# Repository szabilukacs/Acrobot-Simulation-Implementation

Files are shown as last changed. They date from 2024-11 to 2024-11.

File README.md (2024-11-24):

# Acrobot Simulation and Implementation

This repository contains the code and resources for my university thesis, which focused on the simulation and implementation of an **Acrobot** system. The Acrobot is a two-link underactuated robotic arm, commonly used in control theory research. This project bridges theoretical simulations with practical hardware implementation, showcasing the swing-up and stabilization of the Acrobot using Linear-Quadratic Regulator (LQR) control.

https://github.com/user-attachments/assets/334cb275-21a1-4bce-92d3-f9c4527cbd75

---

## 📖 Table of Contents

- [Project Structure](#-project-structure)
- [Features](#️-features)
- [Screenshots and Visuals](#-screenshots-and-visuals)
- [Getting Started](#-getting-started)
- [Results](#-results)
- [Further Details](#-further-details)

---

## 📂 Project Structure

### 1. **Simulations**
   - **Acrobot Swing-Up and Balance Simulation**:
     - A detailed MATLAB/Simulink simulation of the Acrobot, featuring:
       - The ability to modify system attributes, such as:
         - Adding noise to the system to test robustness.
         - Observing simulated data versus simulated encoder data and their differences.
       - A DC motor model implemented in the simulation.
       - Customizable starting positions for the Acrobot.
     - Parameters for the simulation are derived from real-world measurements, but they can be adjusted as needed.

   - **Theoretical Double Pendulum Simulation**:
     - Simulates a theoretical double pendulum to explore its chaotic dynamics and provide insights into the physics and mathematics of such systems.

### 2. **Arduino Implementations**
   - **Encoder Computing**:
     - Reads encoder values to measure the angles of the Acrobot's links in real-time.
   - **Servo Motor Control**:
     - Controls the torque applied to the Acrobot's actuator using a servo motor (replacing the DC motor used in the simulation).
   - **Combined Computing**:
     - Integrates encoder readings and motor control for a closed-loop system in hardware.

---

## 🛠️ Features

- **Simulink Models**: A modular and interactive simulation environment for testing and refining the Acrobot control system.
- **MATLAB Scripts**: Key functionalities include LQR design, energy calculations, and visualization.
- **Hardware Control**:
  - Arduino code for real-time encoder data processing and servo motor actuation.
- **Customization**:
  - Modify system parameters (e.g., masses, lengths, and moments of inertia) based on hardware measurements.
  - Test different starting positions for the Acrobot.

---

## 📸 Screenshots and Visuals

### Simulink Model

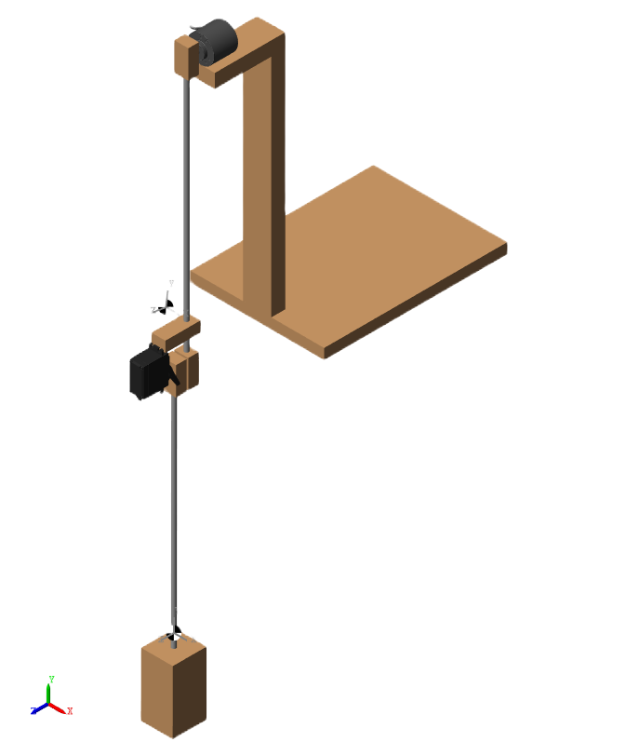
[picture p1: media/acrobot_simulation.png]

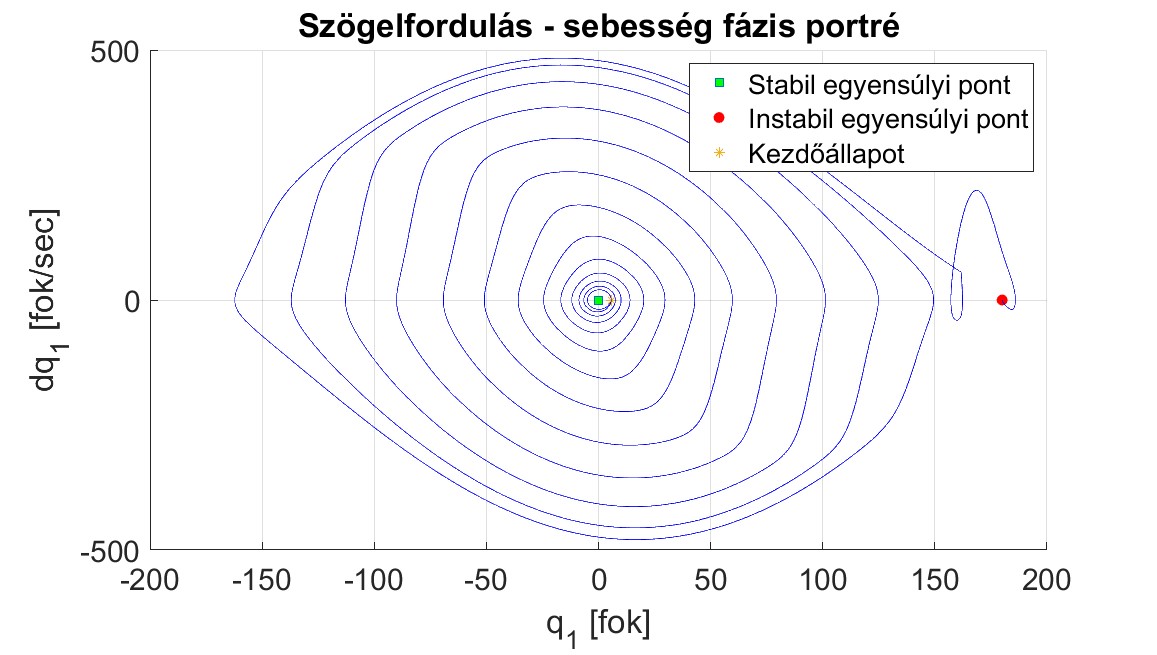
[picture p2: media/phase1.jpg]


### Implementation Setup
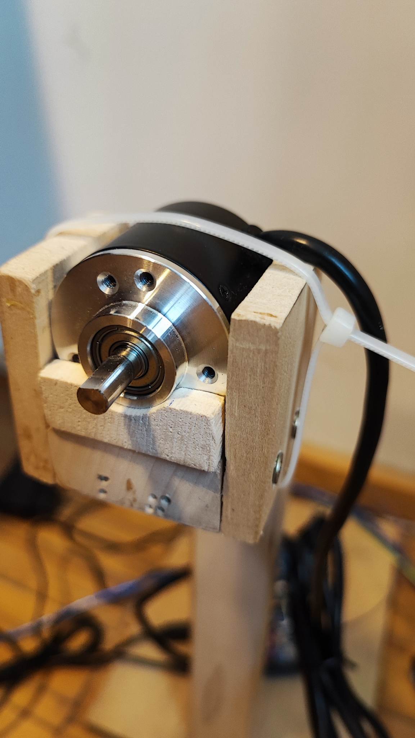
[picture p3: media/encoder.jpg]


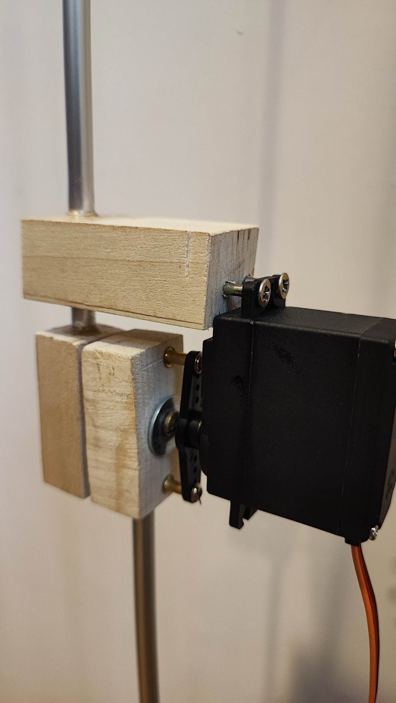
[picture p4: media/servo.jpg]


---

## 🚀 Getting Started

To run the simulation, execute the `main.m` script in MATLAB. This will:
1. Load the system parameters derived from real-world measurements.
2. Linearize the system around the operating point.
3. Perform LQR calculations.
4. Simulate the Acrobot swing-up and balancing behavior in Simulink.
5. Generate visualization plots for analysis.

---

## 📊 Results

### Features of the Simulation
- Observe both ideal simulated data and noisy encoder-like simulated data to analyze differences.
- Test and tune the system under various starting conditions and parameters.

### Hardware Validation
- Parameters in the simulation are based on real-world measurements to ensure accuracy.
- While the simulation uses a DC motor model, the implementation uses a servo motor for torque control.
- The implementation closely follows the behavior predicted by the simulation.

---

## 📜 Further Details

For an in-depth explanation of the project, including theoretical background, implementation details, and results, refer to the thesis document: **`Allamvizsga_szakdolgozat.pdf`**.

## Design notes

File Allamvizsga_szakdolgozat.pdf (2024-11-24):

## UNIVERSITATEA „SAPIENTIA” DIN CLUJ-NAPOCA

FACULTATEA DE ȘTIINȚE TEHNICE ȘI UMANISTE,

## TÎRGU MUREȘ

### SPECIALIZAREA AUTOMATICĂ ȘI INFORMATICĂ APLICATĂ

# REGLAREA ȘI IMPLEMENTAREA PRACTICĂ A UNUI ACROBOT

# PROIECT DE DIPLOMĂ

Coordonator științific: | Absolvent:
Prof.dr.ing. Dávid László | Lukács Szabolcs

2023

UNIVERSITATEA „SAPIENTIA” din CLUJ-NAPOCA | Viza facultății:
Facultatea de Științe Tehnice și Umaniste din Târgu Mureș
Specializarea: Automatică și informatică aplicată
LUCRARE DE DIPLOMĂ
Coordonator științific:
ș.l. dr. ing. Nume cadru didactic

Candidat: Nume student
Anul absolvirii: 2023
a) Tema lucrării de licență:
CONTROLUL AUTOMAT AL SERELOR
b) Problemele principale tratate:
- Studiu bibliografic privind sistemele de reglare.
- Realizarea unei aplicații pentru simularea procesului studiat.
- Clasificarea metodelor de reglare
c) Desene obligatorii:
- Schema bloc al aplicației
- Diagrame UML privind software-ul realizat.
d) Softuri obligatorii:
-Aplicație
e) Bibliografia recomandată:
- Márton Lőrinc, Irányítsátechnika, Scientia, 2009
- Dávid László, Tehnici de optimizare: metode numerice de calcul în tehnica reglării optimale, Editura Universității Petru Maior, Tg. Mureș, 2000,
f) Termene obligatorii de consultații: săptămânal
g) Locul și durata practicii: Universitatea „Sapientia” din Cluj-Napoca, Facultatea de Științe Tehnice și Umaniste din Târgu Mureș
Primit tema la data de: 31.03.2022
Termen de predare: 27.06.2023
Semnătura Director Departament

Semnătura responsabilului
programului de studiu

Semnătura coordonatorului

Semnătura candidatului

Declarație

Subsemnatul Lukács Szabolcs, absolvent(ă) al/a specializării automatică şi informatică aplicată, promoția 2023 cunoscând prevederile Legii Educației Naționale 1/2011 și a Codului de etică și deontologie profesională a Universității Sapientia cu privire la furt intelectual declar pe propria răspundere că prezenta lucrare de licență/proiect de diplomă/disertație se bazează pe activitatea personală, cercetarea/proiectarea este efectuată de mine, informațiile și datele preluate din literatura de specialitate sunt citate în mod corespunzător.

Localitatea, Târgu Mureș
Data: 25.06.2023 | Absolvent
| Semnătura |

# REGLAREA ȘI IMPLEMENTAREA PRACTICĂ A UNUI ACROBOT Extras

Tema tezei mele este implementarea unui sistem de control dinamic neliniar subactuat, și anume un "ACROBOT", care poate fi folosit ca exercițiu de laborator. Controlul sistemelor subactuate necesită un tip de control diferit față de cel al sistemelor convenționale. Scopul meu este de a construi un mecanism experimental pentru a demonstra un astfel de control.

Sistemul dinamic studiat este "acrobotul", care este un pendul dublu inversat, dar care are un dispozitiv de intervenție doar în a doua articulație, deci are două grade de libertate, dar poate interveni doar într-unul dintre gradele de libertate, adică este subactuat.

Scopul principal al controlului este de a muta acrobotul din punctul de echilibru inferior, stabil, în punctul de echilibru superior, instabil, și de a-l stabiliza acolo cu ajutorul unui algoritm de control DLQR. Prin modelarea și simularea precisă a sistemului real, am obținut traiectoria prescrisă a celui de-al doilea segment. Pentru a pune în aplicare acest lucru on-line, adică în timp real, am utilizat o rețea neuronală pentru a mă asigura că unghiul prescris este obținut pe baza stărilor în timp real.

În implementare am folosit un servomotor pentru a deplasa al doilea segment și un encoder incremental pentru a măsura unghiurile și vitezele unghiulare. Prelucrarea semnalului și calcularea semnalului de acțiune se realizează cu ajutorul unor plăci de dezvoltare arduino conectate în rețea.

# SAPIENTIA ERDÉLYI MAGYAR TUDOMÁNYEGYETEM

## MAROSVÁSÁRHELYI KAR AUTOMATIKA ÉS ALKALMAZOTT INFORMATIKA SZAK

# ACROBOT SZABÁLYOZÁSA ÉS GYAKORLATI MEGVALÓSÍTÁSA

# DIPLOMADOLGOZAT

Témavezető: | Hallgató:
Dr. Dávid László, egyetemi tanár | Lukács Szabolcs

2023

# Kivonat

A dolgozatom témája egy olyan nemlineáris, alulaktuált dinamikus rendszer szabályozásának megvalósítása, nevezetesen egy „ACROBOT”, amelyet később laborgyakorlatként is lehet majd használni. Az alulaktuált rendszerek szabályozása másfajta szabályozást igényel, mint a hagyományos rendszereké. Célom egy olyan kísérleti eszköz elkészítése, amin be lehet mutatni egy ilyen szabályozást.

Az tanulmányozott dinamikus rendszer az „acrobot”, ami egy inverz dupla inga, de csak a 2. csuklóban van beavatkozó eszköz, tehát két szabadságfokkal rendelkezik, de csak az egyik szabadságfokban lehet beavatkozni, vagyis alulaktuált.

A szabályozás fő célja eljuttatni az acrobotot az alsó, stabil egyensúlyi pontjáról, a felső, instabil pontjára, és ott stabilizálni felhasználva egy DLQR szabályozási algoritmust. A valós rendszert pontosan modellezve, és szimulálva megkaptam a második szegmens előírt pályáját. Ahhoz, hogy ezt on-line, azaz valós időben lehessen implementálni, egy neuronálót használtam fel, amely biztosítja, hogy a valós idejű állapotok alapján kapjuk meg az előírt szöget.

A megvalósítás során egy szervomotort használok a második szegmens mozgatására, és egy inkrementális enkódert, a szögek és szögsebességek mérésére. A jelek feldolgozása és a beavatkozó jel kiszámítása hálózatba csatolt arduino fejlesztőlapokkal történik.

Kulcsszavak: Acrobot, Alulaktuált rendszer, LQR

# Abstract

The topic of my thesis is the implementation of a nonlinear underactuated dynamic control system, namely an "ACROBOT", which can be used as a laboratory exercise. The control of underactuated systems requires a different kind of control than that of conventional systems. My goal is to build an experimental device to demonstrate such a control.

The dynamic system under study is the "acrobot", which is an inverted double pendulum, but it has an intervention device only in the 2nd joint, so it has two degrees of freedom, but it can only intervene in one degree of freedom, i.e., it is underactuated.

The main purpose of the control is to move the acrobot from its lower, stable equilibrium point to its upper, unstable point and stabilize it there using a DLQR control algorithm. By accurately modeling and simulating the real system, I obtained the prescribed trajectory of the second segment. In order to implement this on-line, in real time, I used a neural network to ensure that the prescribed angle is obtained based on the real-time states.

In the implementation, I use a servo motor to move the second segment and an incremental encoder to measure the angles and angular velocities. The signal processing and the calculation of the action signal is done with networked arduino development boards.

Keywords: Acrobot, Underactuated Systems, LQR

## Tartalomjegyzék

### 10 ÖSSZEGZÉS, KÖVETKEZTETÉSEK | 51 11 IRODALOMJEGYZÉK | 53 12 FÜGGELÉK | 55

## 1 Ábrajegyzék

4.1. ábra. Az acrobot modellje [4] | 13
4.2. ábra. Az Acrobot optimális pályája | 16
5.1. ábra. A szabályzás tömbvázlata[10, p. 12] | 17
5.2. ábra. A nyílt rendszer instabil pólusai | 19
5.3. ábra. A zárt rendszer stabil pólusai | 21
5.4. ábra. A rendszer állapotai szimuláció közben | 22
6.1. ábra. Egy rétegű, egy neuront tartalmazó neuronháló felépítése, az aktivációs függvényeket feltüntetve 25
6.2. ábra. Matlabban megvalósított neuronháló tömbvázlata | 26
6.3. ábra. Tanítóhalmaz (DLQR szabályozás fehér zajjal) | 27
6.4. ábra. A neuronháló kimenete összehasonlítva a kiszámított előírt szöggel | 27
6.5. ábra. Tanítóhalmaz a feltornáztatáshoz (Swing up szabályozás) | 28
6.6. ábra. A neuronháló kimenete és a kiszámított q2 szög összehasonlítása | 29
7.1. ábra. Az acrobot és a szabályzás Simulink modellje | 29
7.2. ábra. A második szegmens Simscape modellje | 31
7.3. ábra. A szabályzó tömbvázlata | 32
7.4. ábra. A neuronhálóval megvalósított szabályzás | 33
7.5. ábra. A szervomotor és a második csukló Simscape modellje | 33
7.6. ábra. Az enkóder és az első csukló Simscape modellje | 34
7.7. ábra. Az acrobot 3D-s modellje szimuláció közben | 35
7.8. ábra. Az acrobot szögeinek és szögsebességeinek változása időben egy sikeres szabályzás alatt | 36
7.9. ábra. A teljes rendszer energiája és a cél energia a szabályozás alatt | 37
7.10. ábra. A szabályzó jel változása Nm-ben a szabályozás közben | 37
7.11. ábra. Az acrobot fázisportréja, az első szegmens szögelfordulása és szögsebesség függvényében.........38
7.12. ábra. Az acrobot 3D-s modellje a felső inverz pontjában | 38
7.13. ábra. Egyenáramú motor szabályozása Simulinkben | 39
7.14. ábra. Ideális és a motor tengelyén megjelenő nyomatékok összehasonlítása | 41
7.15. ábra. Motor áram és feszültség | 42
8.1. ábra. Az acrobot gyakorlati megvalósítása, jobb oldalt a szervomotor és a második csukló | 43
8.2. ábra. Arduino fejlesztőlapokkal megvalósított szabályozás | 44
8.3. ábra. A gyakorlati szabályozás tömbvázlata | 45
8.4. ábra. A forgóérzékelő által küldött A és B jelforma, amikor a forgás az óramutató járásával megegyező
irányban történik[21] | 46
8.5. ábra. A forgóérzékelő által küldött A és B jelforma, amikor a forgás az óramutató járásával megegyező
irányban történik[21] | 46
8.6. ábra. 50Hz-es PWM jel a szervomotor irányításához, feltüntetve a két szélső és a középső állapotához
szükséges kitöltési tényezőt[23] | 48
9.1. ábra. A megvalósított rendszer mérési eredményei szabályozás közben | 50
9.2. ábra. Feltornáztatási fázis összehasonlítása | 51

## 2 Bevezető

Az acrobot egy nemlineáris alulaktuált rendszer. Akkor nevezünk egy rendszert alulaktuáltnak, ha szabadságfokainak a száma nagyobb, mint a rendszer független beavatkozóinak száma. Ez azt jelenti, hogy a rendszernek van néhány "passzív" foka, amelyet nem lehet közvetlenül irányítani az elérhető aktuátorokkal, így nagyon fontos szerepet kap ezen rendszerek szabályozásában a rendszer belső dinamikája.[1] Az alulaktuált rendszerek fontossága abban rejlik, hogy a való életben is számos rendszer alulaktuált. Az alulaktuált rendszerek egyre gyakrabban találhatóak meg a modern robotikában, ilyenek például a sétáló robotok, segway-ek, bipedal robotok, űrbéli robotok, flexibilis robotok, a legtöbb emberi mozgást utánozni próbáló robot.[2] Az egyik legegyszerűbb ilyen rendszer, ezen a területen már alappéldának számító acrobot, ami az emberi járás egyik legegyszerűbb modellje.

Az acrobot esetében 2 szabadságfokról beszélhetünk, és egy beavatkozóról. Ha a beavatkozó az első csuklóban helyezkedik el, akkor pendubotnak nevezzük, ha a másodikban, akkor acrobot. Ha egyik csuklóban sincs beavatkozó, abban az esetben dupla inverz ingáról beszélünk.

Az acrobot esetében a klasszikus szabályozás a robot stabilizálását jelenti a fenti egyensúlyi pontja körül. Általában ezt két részre lehet osztani, az ú.n. “Swing-up” és “Balancing” fázisra[3]. A swing-up fázisban a cél a második szegmens eljuttatása az equilibrium pont környezetébe, a stabilizáló fázis feladata ott tartani és az instabil pontja körül stabilizálni a rendszert.

A dolgozatom célja egy egyszerű acrobot fizikai megvalósítása és annak szabályozása, amely később használható oktatási célra, másfajta szabályozások tanulmányozására. Az acrobot dinamikája eléggé komplex ahhoz, hogy sokféle szabályozási technikát tanulmányozni lehessen rajta.

## 3 Irodalmi áttekintés

Az acrobottal és annak szabályozási nehézségeivel leginkább a ’90-es évek elején kezdtek el foglalkozni. A cél az alulaktuált rendszerek tanulmányozása volt, és az egyik ilyen rendszer az acrobot. Az egyik ilyen cikk, amelyet a későbbiekben sokan idéztek, az Mark.W.Spong [2] cikke, amiben bemutat egy működő szabályozást, az ú.n. ‘swing-up and balance’. Itt az energia pumpálás elvét használja, majd egy LQR szabályozást a linearizált tartományon belüli stabil szabályozásra. A robotot eljuttatja a felső instabil pontjára, majd ott történik egy váltás a két szabályzó között, ami már képes ott stabilan tartani a szerkezetet. Ez volt az egyik legelső és legegyszerűbben leimplementálható szabályozása egy ilyen rendszernek. Egy másik fontos irodalom volt Russ Tedrake MIT kurzus könyve[4], amelyben az acrobot mozgási egyenletei voltak részletezve. Az acrobot mozgásának és szabályozásának a tanulmányozása még a napjainkban is aktív. Manapság másfajta szabályzások megvalósításával foglalkoznak, például optimális pályakövetés, minimum idejű, modell prediktív szabályozások, robusztusabb szabályozások tervezése. Továbbá tanulmányozzák a gépi tanulás eredményeit is, amelyben egy visszacsatoláson keresztül egy valós rendszert is tanítani lehet az egyre pontosabb szabályozás elérésére.[5]

3.1 Gyakorlati megvalósítások

Egy acrobot fizikai megvalósítása a legtöbb esteben nehézkes. Két fő részre oszthatók: „Directly driven acrobot” (DDA) és „Remotely driven acrobot” (RDA).[6]

3.1.1 RDA (Remotely Driven Acrobot)

A második szegmens meghajtása egy vezérműszíjon keresztül van meghajtva, így elérve, hogy az aktuátor nem mozog együtt az egész rendszerrel, hanem egy fix ponthoz rögzítve tudja vezérelni a második szegmenst. Előnye, hogy a motor súlya nem terheli a rendszert, így a szegmensek könnyebb anyagból is készíthetők, és nagyobb nyomaték is kifejthető, az áttételnek köszönhetően. Hátránya a fizikai megvalósításban a bonyolultabb felépítés, az áttételek megoldása és stabilan tartása a robot teljes mozgási tartományán belül. A gyakorlatban ez az elterjedtebb modell az acrobot bemutatására.

3.1.2 DDA (Directly Driven Acrobot)

A directly driven acrobot esetében közvetlenül van meghajtva a második szegmens. Ebben az esetben a motor, vagy a beavatkozó közvetlenül hajtja meg a második szegmenst. Kevésbé elterjedt, mivel itt korlátozottak a rendszer paraméterei. Ha túl nagy a motor tömege, akkor a második kar végén lévő súlyt is növelni kell, hogy fel lehessen tornásztatni az inverz állapotába. Ha viszont nagyobb az alsó súly, az általában nehezebb, drágább motorhoz vezet, mivel nagyobb nyomaték lesz szükséges ennek mozgatására. Előnye viszont, hogy egyszerűbb fizikai felépítéssel is kivitelezhető.

A fenti előnyöket és hátrányokat figyelembe véve a DDA mellett döntöttem, mivel manapság már elérhetőek kellően könnyű és viszonylag nagy maximális kifejthető nyomatékkal rendelkező szervomotorok. Így kevésbé komplex mechanikai kivitelezésben is megvalósítható a rendszer.

## 4 Az acrobot dinamikája

Az acrobot egy két szabadságfokkal rendelkező, úgynevezett dupla, kétszeresen csatolt inga. A felfüggesztéshez közelebbi csuklót sokszor nevezik vállnak, a távolabbit, ahol az aktuátor jelen van, könyöknek.[4] Ez a (4.1. ábra)-n τ-val jelölve látható a beavatkozó nyomaték, illetve az 1. táblázat.-ban az ábrához tartozó jelmagyarázat, benne a modellezés során is felhasznált összes paraméterrel. A szabályozási nehézséget az adja, hogy figyelembe kell venni az állapotfüggő kapcsolatot az aktív és a passzív szabadságfokok közt.

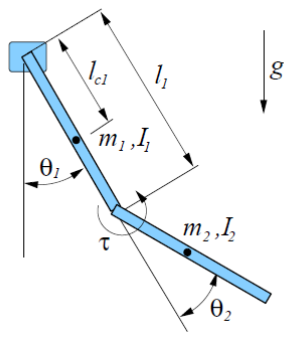
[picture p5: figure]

### 4.1. ábra. Az acrobot modellje [4]

A szegmensek tehetetlenségi nyomatéka:[7] II =

1

# 12 mmll2

( 1 )

τ | nyomaték
l1 | Első szegmens hossza
l2 | Második szegmens hossza
lc1 | Első szegmens tömegközéppontjának hossza
lc2 | Második tömegközéppontjának hossza
m1 | Első szegmens tömege
m2 | Második szegmens tömege
g | Gravitációs állandó
θ1 | Első szegmens relatív elfordulása
θ2 | Második szegmens relatív elfordulása
I1 | Első szegmens inerciája
I2 | Második szegmens inerciája

### 1. táblázat. Jelmagyarázat

4.1 Mozgásegyenletek

A mozgásegyenletek a könnyebb átláthatóság kedvéért a Lagrange mechanika alapján vannak levezetve.[4]
x1 x2 jelöli az abszolút helyét az első és a második szegmens tömegközéppontjának.

# xx1 = llcc1 ∗ sin (q1) −llcc1 ∗ cos(qq1)

# xx2 = xx1 + ll2 ∗ sin (qq1 + qq2) −ll2 ∗ cos (qq1 + qq2)

( 2 )
Így az acrobot mozgási energiája P, ami két részből tevődik össze.

PP1 = 1
2

# ∗ II1 ∗ qq1

2̇

( 3 )

PP2 = 1

# 2 ∗ (mm2 ∗ ll1

# 2 + II2 + 2 ∗ mm2 ∗ ll1 ∗ llcc2 ∗ cos(qq2)) ∗ qq1

2̇ +

1
2

# ∗ II2 ∗ qq1

2̇

# + (II2 + mm2 ∗ ll1 ∗ llcc2 ∗ cos(qq2)) ∗ qq1

2̇ *qq2

2̇

( 4 )
Mozgási energia

# PP = PP1 + PP2

( 5 )

Potenciális energia

# KK = −mm1 ∗ gg ∗ llcc1 ∗ cos(qq1) − mm2 ∗ gg ∗ (ll1 ∗ cc1 + ll2 ∗ cos (qq1 + qq2)

( 6 )
A Lagrange függvény

# LL = PP – KK

( 7 )
Kiszámítva a parciális deriváltakat, [8] majd behelyettesítve az Euler-Lagrange-egyenletbe(8),[9]

dd
dddd

∂∂
∂∂qq̇

−

∂∂
∂∂ = ττ

( 8 )
megkapjuk a mozgási egyenleteket. Ezeket rendszerezve kapjuk az acrobot mozgását leíró mátrixokat.[4]

# MM(qq) =

# II1 + II2 + mm2ll1 2 + 2mm2ll1ll 2cos (qq2) II2 + mm2ll1ll 2cos (qq2) II2 + mm2ll1llcc2cos (qq2) II2

( 9 )

# CC(qq, qq̇) =

# −2mm2ll1ll 2 sin(qq2) qq2̇ −mm2ll1ll 2sin (qq2)qq2̇ mm2ll1llcc2sin (qq2)qq1̇ 0

( 10 )

# GG(qq) =

# mm1gg cc1sin (qq1) − mm2gg(ll1 sin(qq1) + llcc2sin (qq1 + qq2)) mm2gg cc2sin (qq1 + qq2)

( 11 )
Ahol:
M - tehetetlenségi mátrix
C - Centrifugális és a Coriolis erők vektora
G - a gravitációs erő hatása
Összeségében a következőképpen írható fel az acrobot dinamikus modellje:

# MM(qq)qq̈+ CC(qq, qq̇) + GG(qq) = BBBB

( 12 )

Ahol az acrobot esetében
BB =

0
1

( 13 )
Csak az egyik bemenet aktív, mivel csak a második csuklóban van a beavatkozó.

4.2 Az optimális pálya

Az acrobot optimális pályája alatt, ebben az esetben azt értjük, amikor a rendszer a legkisebb nyomaték kifejtésével tud eljutni az alsó egyensúlyi pontjáról a felső, instabil pontjára. Az 5.2.-ben részletezett szabályozás nem optimális pályát követ, hanem a folyamatos energia pumpálás módszerével juttatja el az acrobotot a felső pontjára. Bebizonyítható, hogy nem ez az optimális pálya, viszont ez a módszer valósítható meg a legmegbízhatóbban, és a valós időben.

Az | acrobot | optimális | pályájának
kiszámításához az optimTraj[10] nevű
Matlabban futtatható programot használtam.
A program által kiszámított pálya a

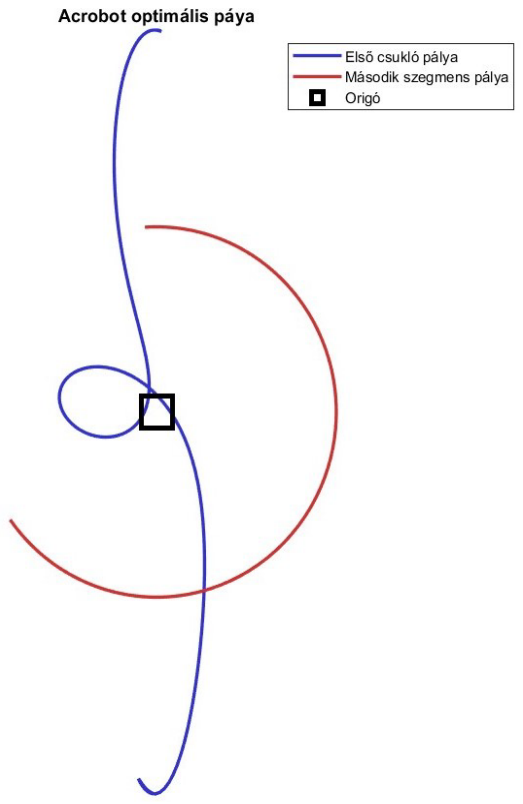
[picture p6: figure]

(4.2. ábra.)-n látható. A könnyebb átláthatóság érdekében az első és a második szegmens végpontja által leírt pálya látható. A számításokban a valós rendszer paramétereit használtam. Megfigyelhető, hogy ebben az esetben a súlyt elég volt egyszer, viszont nagy nyomatékkal belendíteni, és az már elegendő volt ahhoz, hogy a teljes szerkezetet eljuttassa a felső egyensúlyi állapotába. A programba be vannak vezetve a 4.1. fejezetben levezetett mozgási egyenletek, ebben az esetben a költségfüggvény a nyomaték négyzete. Az algoritmus a differenciálegyenletek megoldására a negyedrendű Runge-Kutta módszer alkalmazza.

### 4.2. ábra. Az Acrobot optimális pályája

## 5 Szabályzó

A rendszer nemlineáris jellegéből adódóan a szabályzási feladatot nem lehet megoldani csak egy lineáris szabályzóval. Ennek megoldására többféle módszer is létezik, például olyan szabályzási algoritmusok, amelyek lefedik a teljes, globális mozgási tartományt, ilyenek például a neuronhálóval megoldott szabályozások, részleges linearizálást alkalmazó szabályzások vagy két egymástól különböző szabályzó hibrid alkalmazása.

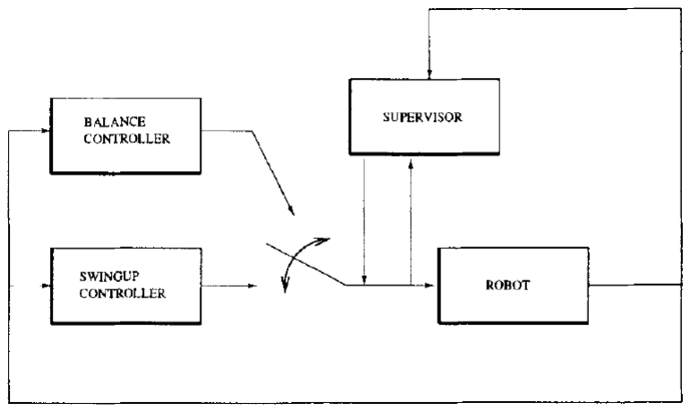
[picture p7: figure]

### 5.1. ábra. A szabályzás tömbvázlata[11, p. 12]

Az elv az, hogy az acrobotot eljuttatjuk az elvárt egyensúlyi pontja közelébe, úgy, hogy megfelelő állapotok szerint érje el azt. Azután egy másik kontroller veszi át az irányítást, amely ott tartja, stabilizálja az egyensúlyi pontja körül. Amint az 5.1. ábrán látható a rendszer állapotát egy egység folyamatosan figyeli, és ezek függvényében kapcsol át a két különböző szabályzó között. Ideális esetben csak egyszer kell átváltani a stabilizálást végző szabályzóra, viszont amennyiben ez zajok miatt nem lett volna sikeres, akkor a kapcsoló visszavált és folytatja tovább a rendszer feltornáztatását.

5.1 Lineáris szabályzó

Ahhoz, hogy alkalmazni tudjuk az LQR szabályzót, linearizálni kell a rendszert a felső egyensúlyi állapota körül (UEP). Az UEP közvetlen környezetében sikeresen fog tudni működni a lineáris szabályzó, mivel az eltérések a nemlineáris és a lineáris rendszer között minimálisak.[2]

UEP pont:

# qq1 = pppp, qq2 = 0, qq1̇ = 0, qq̇

22 = 0

( 14 )
5.1.1 Linearizált modell

A linearizált modellt a következő alakban tudjuk felírni.

# xẋ = AA ∗ xx + BB ∗

( 15 )
Ahol az A mátrix a rendszermátrix és B mátrix a bemeneti mátrix. Linearizálva a rendszert a [12] szerint és behelyettesítve a valós paramétereket:
AA =

0 0
0 0

1 0
0 1
28.0744 −34.4596
−31.7716 95.9008

0 0
0 0

BB =

0
0
−168.3284

407.3343

( 16 )
A C 4x4 egységmátrix és D 4x1 méretű null-mátrix.

5.1.2 Diszkretizálás

Mivel a valóságban diszkrét értékekkel kell megvalósítani a rendszer szabályozását, ezért diszkretizáltam a rendszert. A diszkrét rendszerre való áttérést a nulladrendű tartó módszerrel végeztem. Mintavételezési idő Ts = 20 ms.

A kapott diszkrét rendszer:
AA =

1.02 −0.02
−0.02 1.078

0.04 0
0 0.04
1.14 −1.42
−1.31 3.94

1.02 −0.02
−0.02 1.07

BB = −0.13
0.33
| −6.93

16.77

( 17 )
5.1.3 Szabályozhatóság vizsgálata

A nyílt rendszer nem stabil, ami várható volt, mert az instabil egyensúlyi állapota körül linearizáltuk. A rendszer pólusai közül kettő is az egységsugarú körön kívül van (5.2. ábra).

### 5.2. ábra. A nyílt rendszer instabil pólusai

A rendszer teljesen irányítható, ha az irányíthatósági mátrixának rangja egyenlő a rendszermátrix n-el, tudva, hogy Anxn méretű.[13, p. 145]

A rendszer rangja 4, ugyan úgy, mint az irányíthatósági mátrixé tehát irányítható a rendszer.

5.1.4 DLQR szabályzó

A munkapont körül linearizált diszkrét rendszerre[12] lehet alkalmazni a discrete linear quadratic regulator algoritmust. Ehhez meg kell oldani a diszkrét Ricatti egyenletet[14]. A diszkrét Ricatti egyenlet megoldását (P mátrix) a diszkrét Schur módszert alkalmazva kaptam meg.

Ezután a K erősítésvektor megkaphatjuk

# KK = ((RR + BB′PP )BB′PP )−1

( 18 )
Ahol Q 4x4 méretű egységmátrix, R = 100 választva.

KK = [−9.21 −3.02 −2.36 −0.91]

( 19 )
A szabályzójel számítása:

# = −KK ∗ xx

( 20 )
Ahol x állapotokat jelöli.

# xx = [qq1 qq2 qq1̇ qq2̇ ]

( 21 )
A zárt szabályzási kört megkaphatjuk, ha az A rendszermátrixból kivonjuk a K erősítésvektor által súlyozott bementi B mátrixot.
A szabályozott rendszer sajátértékei, vagyis pólusai az egység sugarú körön belül vannak, tehát látható, hogy a rendszer stabil (5.3. ábra).

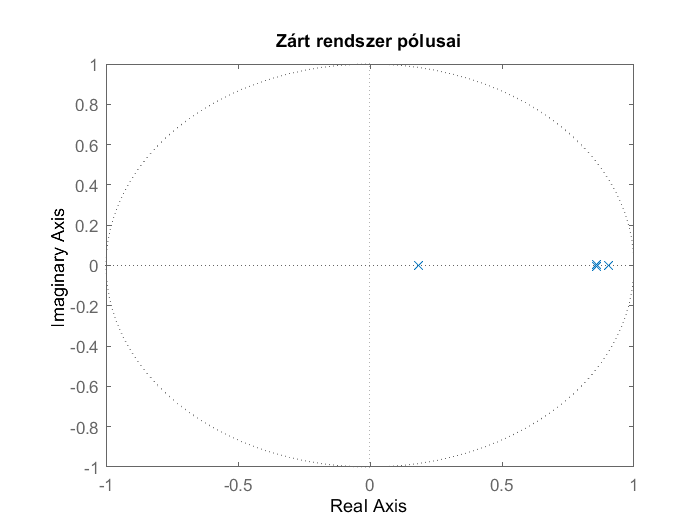
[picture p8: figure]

### 5.3. ábra. A zárt rendszer stabil pólusai

Szimulálva a rendszert látható, hogy az állapotokat a 0-ba vezeti a rendszer. (5.4. ábra.)

A szimulációhoz használt kezdőállapot radiánban:
xx0 = [0.02 −0.04 0 0]

( 22 )

### 5.4. ábra. A rendszer állapotai szimuláció közben

5.2 Energia alapú szabályozás

Az energia alapú szabályozás elve, hogy a rendszerbe energiát pumpálunk, azzal, hogy a második szegmenst az első szegmens szögelfordulása és gyorsulása alapján kilengessük. Lényegében be kell lengetni a rendszert, addig amíg eléri a felső egyensúlyi pontját. Ezzel a módszerrel folyamatosan mozgási energiát viszünk be a rendszerbe.[3] A feladat, hogy a kezdeti [0 0 0 0] állapotából eljuttassuk a [pi 0 0 0] állapotba.

Az alapötlet az, hogy a belengetjük a második szegmenst egy rögzített ±α szög között, akkor amikor az fázisban van, úgy, hogy az amplitúdója az első szegmens kilengésének minden lengéssel növekedjen. A legegyszerűbb stratégia akkor lengetni a szegmenst, amikor a qq1̇ null-átmenetben

van.

Ennek megvalósítására ilyen függvény például a szaturációs függvény[3]. Ennek egy kifinomultabb változata az arcus tangens függvény.
qq2

# dd = (2αα/ππ) tan−1(qq1)̇

( 23 )
Ezt vezérlőjelként kiadva kp és kd erősítési tényezőkkel végezzük, ahol a kp az ideális pálya és az aktuális pálya közti eltérést erősíti, kd pedig a gyorsulást.[3]

# = kkppqq2

# dd − qq2 − kkddqq2̇

( 24 )
Ahhoz, hogy a belengetés időben is hatékony legyen, és a felső inverz pontot is közel nulla sebességgel érje el a következő értékeket alkalmaztam a szabályzáshoz:

# αα = 1 [rrrr ], kkpp = 450 kkdd =0.3

( 25 )
5.3 Switch logic

A két szabályzó között csak a megfelelő állapotban szabad váltani. Fontos, hogy az UEP pontot lehetőleg minimális szöggyorsulás mellett érje el. A feltételt, ahol a szabályzó átválthat a legtöbb esetben empirikus módon határozzák meg. A következő feltételt vettem alapul.[15, p. 15]

# |qq1| + |qq2| + 0.1|qq1̇ | + 0.1|qq2̇ | < ξξ

( 26 )
Sokszor azonban az átváltás pillanatában a lineáris szabályzó kezdeti beavatkozó jele nagyon nagy lehet, amit a fizikai rendszerben már nem lehet megvalósítani. Ennek elkerülésére én figyelembe vettem a lineáris szabályzó jelét is. Ahhoz, hogy a rendszer sikeresen tudjon váltani a két szabályzó között a DLQR szabályzó jele is egy határon belülre kell kerüljön. A feltétel a váltásra így a következőképpen alakult

# |qq1| + |qq2| + 0.1|qq1̇ | + 0.1|qq2̇ | + | | < ξξ

( 27 )

Ahol az u a lineáris szabályzó által kiszámított szabályzójel. Az ξ értéke, amelynél a szabályzó sikeresen átválthat 1.6.

Fontos, hogy az átváltás után megtörténhet, hogy a fenti feltétel újra nem teljesül kilengések miatt, ügyelni kell arra, hogy ne váltsunk vissza a feltornáztatáshoz használt szabályzóra. Különbséget kell tenni a sikertele szabályozás és az ideiglenes kilengések között úgy, hogyha sikertelen, akkor térjen vissza az acrobot feltornásztatásához. Ehhez egy felsőbb limitet választottam ξ = 15. Ezt meghaladva a váltó logika sikertelennek veszi a lineáris tartományban a szabályzást és visszavált az első fázisban használt szabályzóra.

## 6 Neuronháló

Mivel a szabályozást valós környezetben is megkell valósítani, így törekedtem az egyszerű kivitelezésre, olyan számításokra, amelyeket egy mikroprocesszoron is el lehet végezni. A szervomotornak egy előírt szöget kell megadni és nem nyomatékot, tehát a szabályzó jel kiszámítása után (ami egy erő, nyomatékban kifejezve) ahhoz, hogy megkapjam az előírt szöget, valós időben kéne szimulálni a rendszert, kiintegrálni a mozgási egyenleteket. A szimuláció alapján kigenerált szabályzó jelet kiadva a valós rendszernek csak off-line irányítást kapnánk, mivel nincs visszacsatolás, nem vesszük figyelembe az állapotokat. Ahhoz, hogy on-line szabályozás legyen, és elkerüljem a nagy számítási igényt az előírt szög kiszámítására, ezért alkalmaztam egy MLP típusú neuronhálót. A neuronhálót a Simulinkben elvégzett szimuláció alapján tanítottam, a mért q1 és qq1̇ állapotok szerint

tudja kiszámítani a második szegmens előírt szögét. A szervo szabályozás erre az előírt szögre kell vezérelje a motort. Két neuronhálót alkalmaztam külön a két szabályzóra. A neuronháló előnye, hogy a betanítás után nagyon kevés számítási időt igénylő számításokkal is elérhető egy olyan szabályozás, ami a rendszer állapotai függvényében számolja ki az előírt szöget. Viszonylag nagy pontossággal sikerült megtanulja az összefüggéseket, még úgy is, hogy csak a passzív csukló állapotai vannak mérve a valós rendszeren, tehát a betanítás is csak ezek alapján történt.

6.1 Egyrétegű előrecsatolt neuronháló felépítése

A neuronháló 3 fő részre osztható, az első a bemeneti réteg, amely továbbítja az adatokat a háló többi részéhez. A második a rejtett réteg, amely egy neuront tartalmaz, és a harmadik a kimeneti réteg. Két bemeneti neuron van, mivel két állapotot mérünk, a szögelfordulást és a szögsebességet.

Egy kimeneti neuron található, mivel egy vezérlőjelet kell kiszámítsunk. A neuronháló bemenetén az adatokat előfeldolgozni kell, így az eltolt, és skálázott értékek kerülnek a rejtett rétegre.

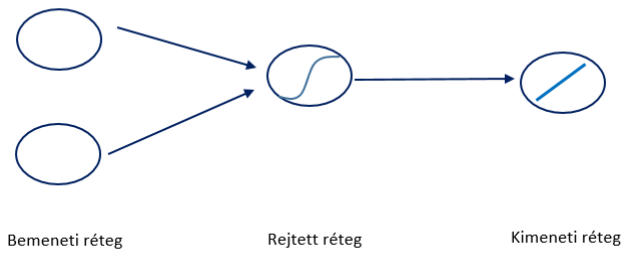
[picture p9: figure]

6.1. ábra. Egy rétegű, egy neuront tartalmazó neuronháló felépítése, az aktivációs függvényeket feltüntetve

6.2 Megvalósítás

A megvalósítás a Matlab feedforwardnet[16] beépített függvénnyel és az ahhoz kapcsolódó funkciókkal történt. A tanításhoz a Levenberg-Marquardt algoritmus használtam, a hibaszámolás az átlagos négyzetes eltérés szerint történik. A rejtett réteg aktivációs függvénye tansig, a kimeneti rétegé purelin aktivációs függvény.

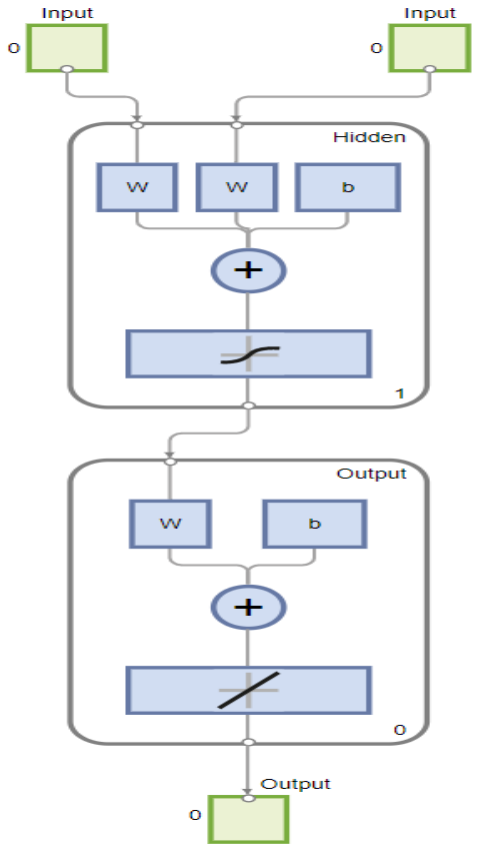
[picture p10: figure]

### 6.2. ábra. Matlabban megvalósított neuronháló tömbvázlata

6.2.1 DLQR

A 6. fejezetben szimuláltam le a szabályozást. A kezdőállapotokat a lineáris tartomány szélére érdemes választani, amelyekre még sikeres a lineáris szabályzó, hogy a tesztjelek, amikre tanítom a neuronhálót, minél nagyobb tartományt fedjenek le. A rendszerre egy konstans fehér zajt és 3 előre meghatározott pontba egy nagyobb zajt is adtam, amelyek célja az volt, hogy valósághűbb legyen a szimulált szabályozás és minél aktívabb legyen a szabályzó, így több hasznos adatot generálva a tanítóhalmazhoz.

Az (6.3. ábra.) ábrán látható a DLQR szabályzót alkalmazva az első szegmens időbeli szögelfordulása és szögsebessége. Mivel a DLQR szabályozás a (a 4.1. ábra szerinti koordináta rendszerben) π radián értékre kell eljuttassa az első állapotot, ezért a neuronhálónak is így adtam meg az adatokat, π radiánnal eltolva. A könnyebb átláthatóság kedvéért ezeket az értékeket ábrázoláskor a továbbiakban átalakítottam fok, illetve fok/másodperc mértékegységekké.

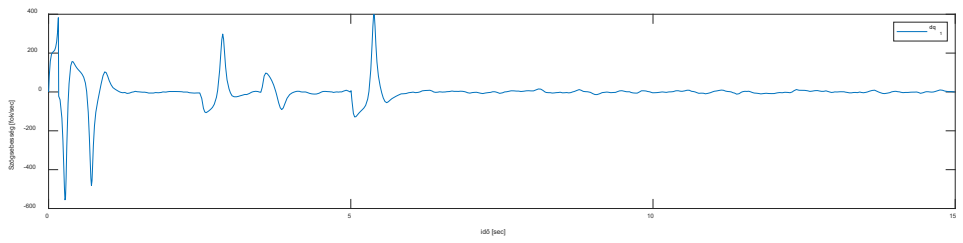
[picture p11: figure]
idő [sec]; Szögsebesség [fok/sec]

### 6.3. ábra. Tanítóhalmaz (DLQR szabályozás fehér zajjal)

A (6.4. ábra) ábrán látható a tanítás eredménye. Látható, hogy sikeresen megtudta tanulni az összefüggést az első szegmens állapotai és az előírt szöge között. A legnagyobb eltérések 3-5 ° közöttiek, amelyek csak a gyors, intenzív beavatkozásoknál jelennek meg, viszonylag kevés ideig.

### 6.4. ábra. A neuronháló kimenete összehasonlítva a kiszámított előírt szöggel

A kiszámított előirt szög és a neuronháló kimenete

6.2.2 Swing up

A swing-up, vagyis feltornáztató fázisra is ugyan azt a neuronháló felépítést és tanítási algoritmusokat alkalmaztam. Leszimulálva egy sikeres feltornásztatást, és nem átkapcsolva a DLQR szabályzóra
(5.1.4) megkaptam egy az 6.5. ábra alsó felében látható q2 pályát időben. Ezt a pályát követve a valós rendszer is fel kell tudja tornáztatni magát az UEP pontjának közelébe. Az 6.5. ábra első grafikonján látható, hogy a szabályzó sikeresen eléri a 180°-ot 25 másodperc után, viszont ott nem tudja megtartani magát, ilyenkor kell majd alkalmazni, az ezen a tartományon pontosabb DLQR szabályzót.

Mivel a valós rendszeren is a [-2π, 2π] tartományban dolgozik a szabályzó, így a tanítóhalmazban is ezen a tartományon belülre korlátoztam a szögeket. Ilyen abban az esetben fordulhatott elő, ha akár többször is körbe fordult az acrobot. Ez látható a 28. másodperc után.

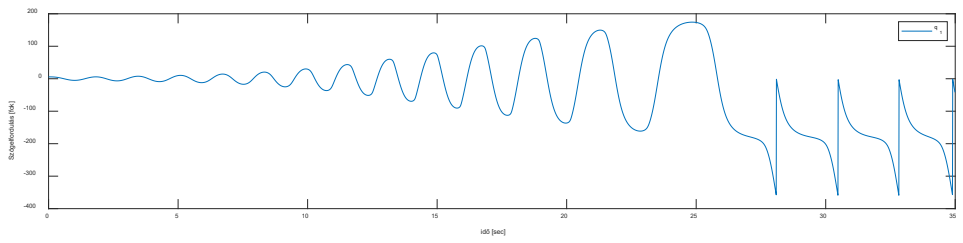
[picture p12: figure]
idő [sec]; Szögelfordulás [fok]
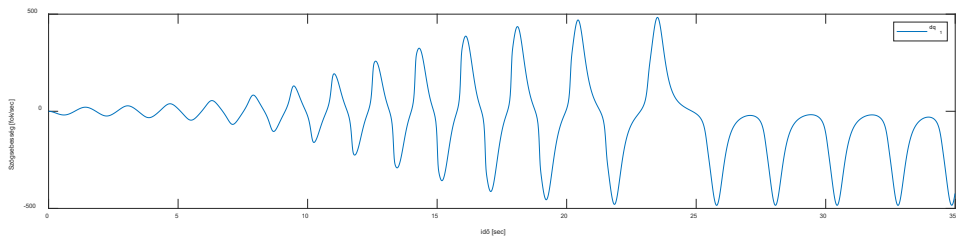
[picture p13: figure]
idő [sec]; Szögsebesség [fok/sec]

### 6.5. ábra. Tanítóhalmaz a feltornáztatáshoz (Swing up szabályozás)

A tanitás eredménye látható a (5.6. ábra) ábrán. A legnagyobb különbség az előírt q2 szögpálya és a neuronháló által kiszámított között, 2°, tehát a tanulás itt is sikeresnek bizonyult.

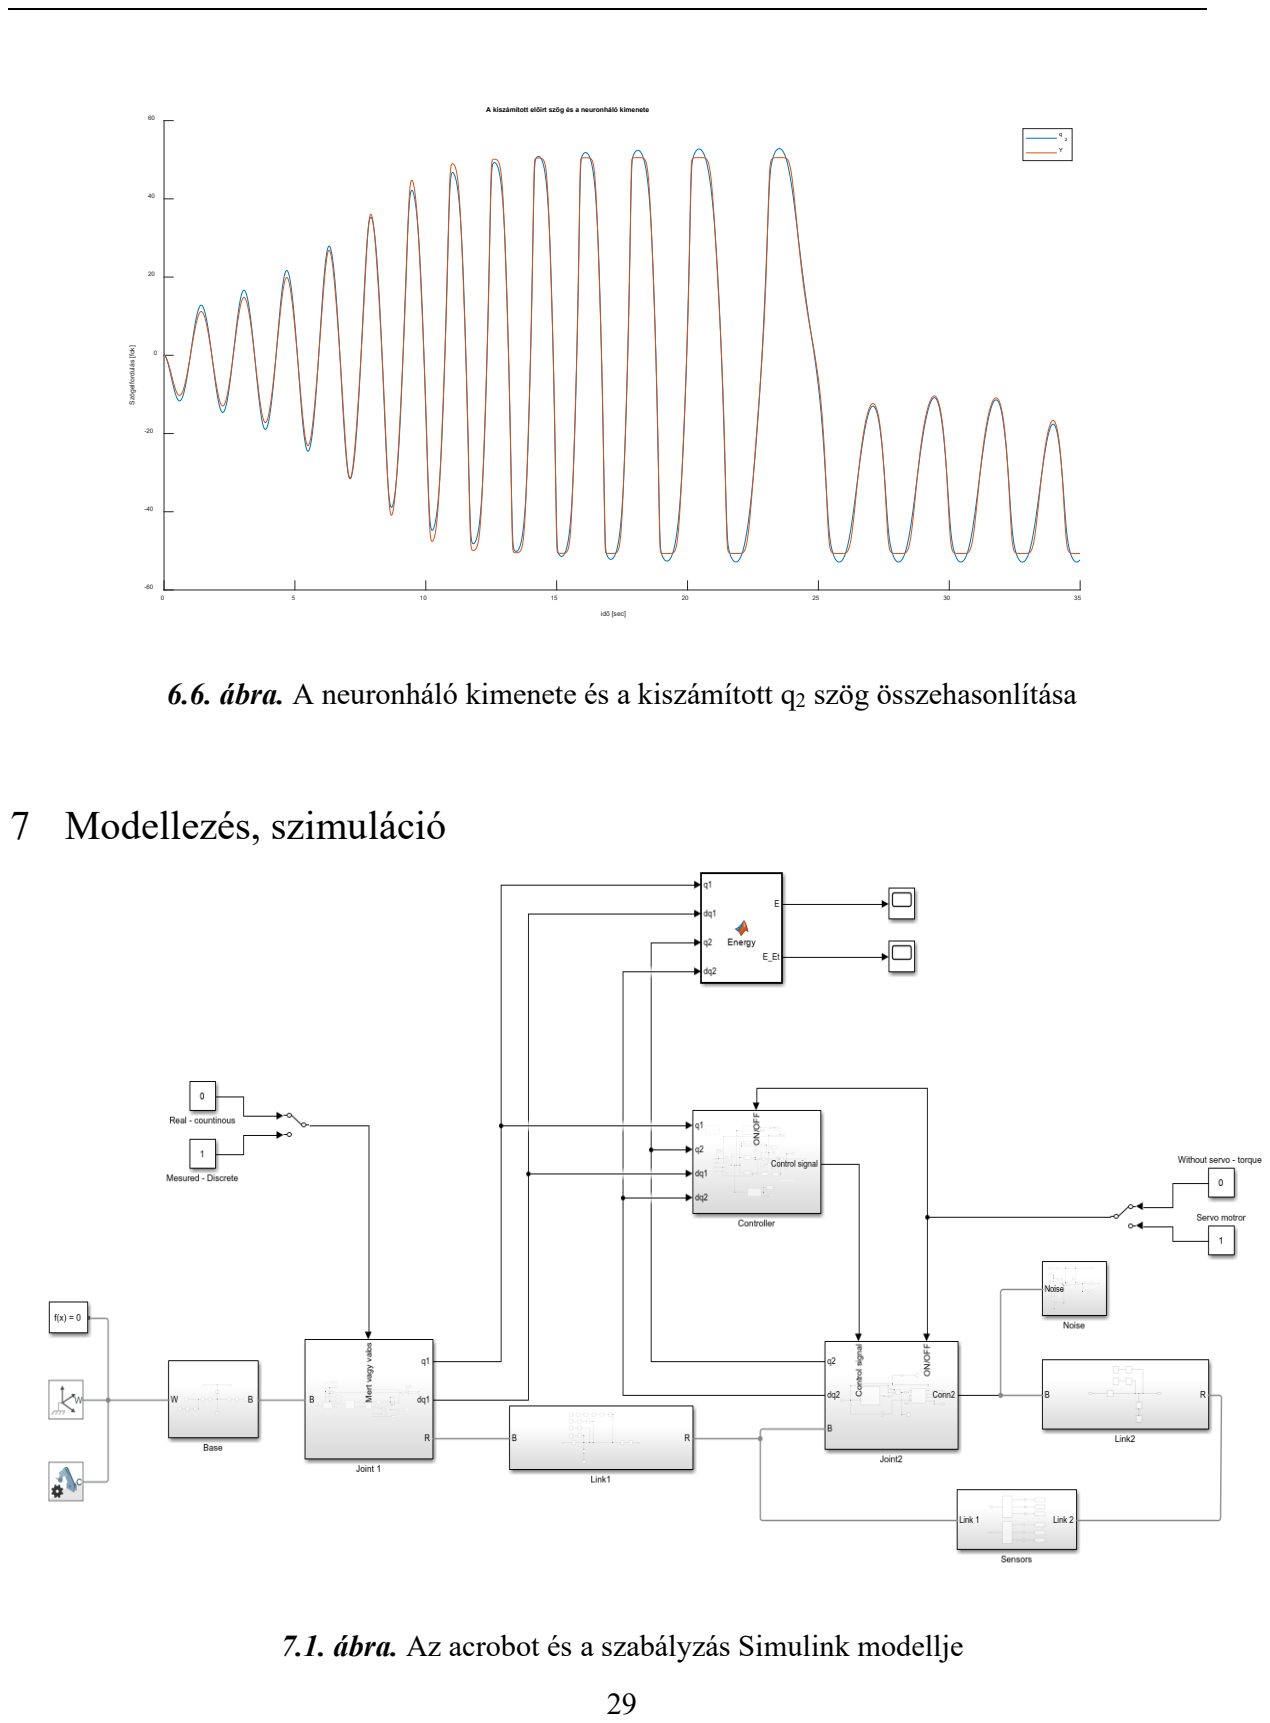
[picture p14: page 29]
7 Modellezés, szimuláció; idő [sec]; Szögelfordulás [fok]

A kiszámított előirt szög és a neuronháló kimenete

6.6. ábra. A neuronháló kimenete és a kiszámított q2 szög összehasonlítása

7.1. ábra. Az acrobot és a szabályzás Simulink modellje

A modellezésre a Simulink-hez tartozó Simscape[17] csomagot használtam, simulink elemekkel egybekötve. A simscape egy különálló szoftvercsomag a Simulinken belül, amely a fizikai elemek modellezésére szolgál. Ennek segítségével hoztam létre az acrobot 3D-s modelljét, megadva a pontos paramétereket. Ezek a következő alrendszerek: Base, Joint1, Link1, Joint2, Link2, amelyek a (7.1. ábra) ábrán láthatóak. A Sensors nevű alrendszerben mérem külön a két szegmens egyes paramétereit, mint például az össztömeg vagy az inercia. A Noise alrendszerben találhatóak a zaj generáláshoz szükséges elemek, amelyek a második szegmensre hatnak. Látható, hogy a Controller tömb megkapja a rendszer állapotait, majd a vezérlőjelet kiszámítva hat a második, aktív csuklóra. A jobb oldalon látható kapcsolóval lehet választani, hogy a második csuklót direktben nyomatékkal vezéreljük, vagy beiktassuk a szervomotort, azáltal megvezérelve a második csuklót. A baloldalon található kapcsolóval lehet állítani, hogy a szabályzó a Simulink által mért szögeket és szöggyorsulásokat használja, vagy a diszkért, forgójeladó (incremental rotary encoder) által kiszámított értéket. Ezzel a megvalósítással lehet tanulmányozni, hogy a forgójeladó pontossága, hogyan hat a számításokra, itt megtalálható egy dekóder is, ami az enkóder által szolgáltatott jelekből kiszámolja a szögelfordulást és a szögsebességet. Fent látható a rendszer energiáját kiszámító Simulink tömb, amely a [15, p. 3]szerint számolja ki a rendszer pillanatnyi energiáját. A második kimenetén található a cél energia (0 mozgási energia és potenciális energia a felső invertált helyzetében) és az aktuális energiája közti eltérés. A szimuláció az ode23t[18] módszert használja numerikus integrálásra, amely egy időlépéses, adaptív integráló algoritmus, amely ebben az esetben hatékonyabbnak bizonyult, mint az ode45. A paraméterek kiszámítását, a szimuláció elkezdését, majd az eredmények megjelenítését Main (4.függelék) program fogja össze.

7.1 A modell felépítése

7.1.1 Fizikai elemek

A Simscape csomag által könnyen meglehet adni a fizikai elemek tulajdonságait, mint a méretük, tömegük. Könnyedén és alrendszerekre bontva le lehet modellezni az egész robotot ezáltal.

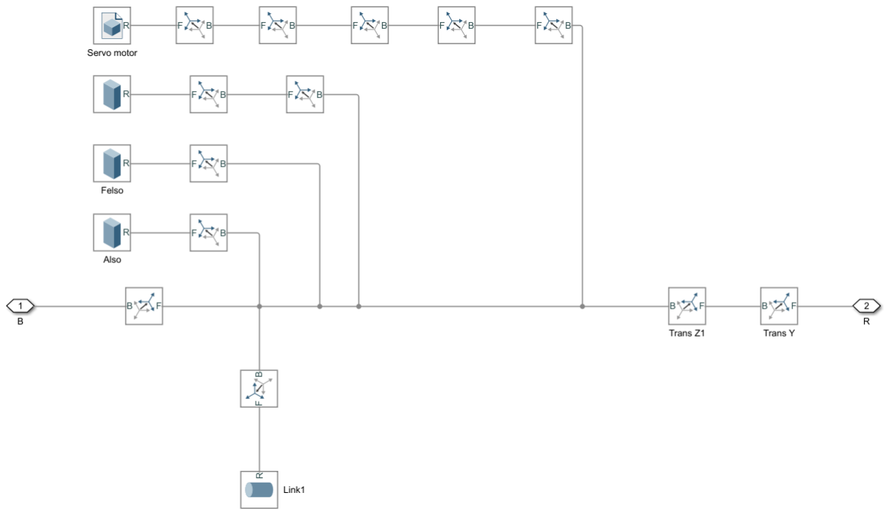
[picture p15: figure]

### 7.2. ábra. A második szegmens Simscape modellje

A (7.2. ábra) ábrán látható a második szegmens fizikai modellje. Megtalálható a rúd, a végén lévő összekötő elemek, és a szervomotor 3D-s modellje is.[19]

7.1.2 Szabályzó

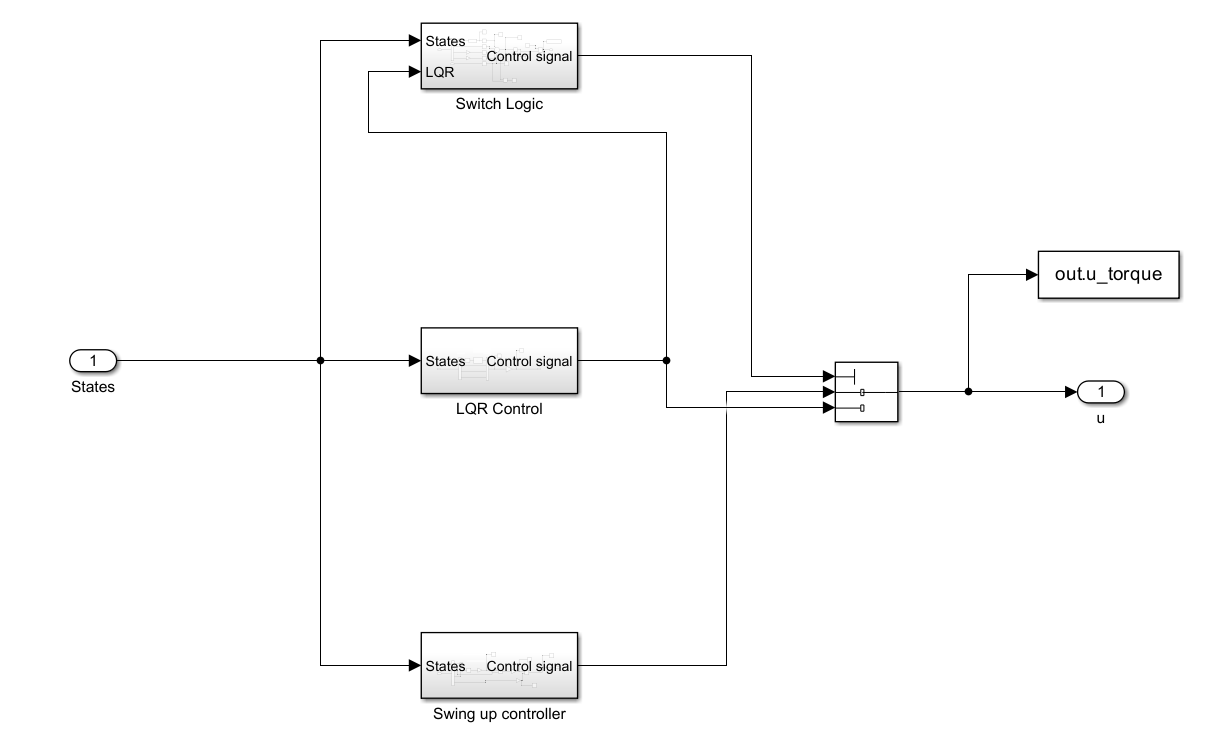
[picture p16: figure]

### 7.3. ábra. A szabályzó tömbvázlata

A szimulációban megtalálható mind a DLQR és energia alapú szabályzó (7.3. ábra), mind ennek a neuronhálóval való implementálása (7.4. ábra). A neuronhálók Simulink modelljét, vagyis az adatok feldolgozását, majd a súlyokkal való szorzását a tanítás után a gensim beépített függvénnyel generáltam ki.

### 7.4. ábra. A neuronhálóval megvalósított szabályzás

7.1.3 Szervomotor

### 7.5. ábra. A szervomotor és a második csukló Simscape modellje

A Servo Motor alrendszerben található a szervomotor Simscape modellje, a valóságban is használt szervomotor katalógus adatai szerint. Itt látható az ON/OFF kapcsoló szerepe is, amely vagy direktben a vezérlő jellel hat a csuklóra, ami nyomatékban van kifejezve, vagy a szervomotor által szolgáltatott nyomaték mozdítja el a második szegmenst. Ebben az esetben a vezérlőjel egy előírt szög kell legyen, amit majd a szervomotor követ.

7.1.4 Forgóérzékelő

Az első csuklóban található a forgóérzékelő, vagyis az incremental rotary encoder.

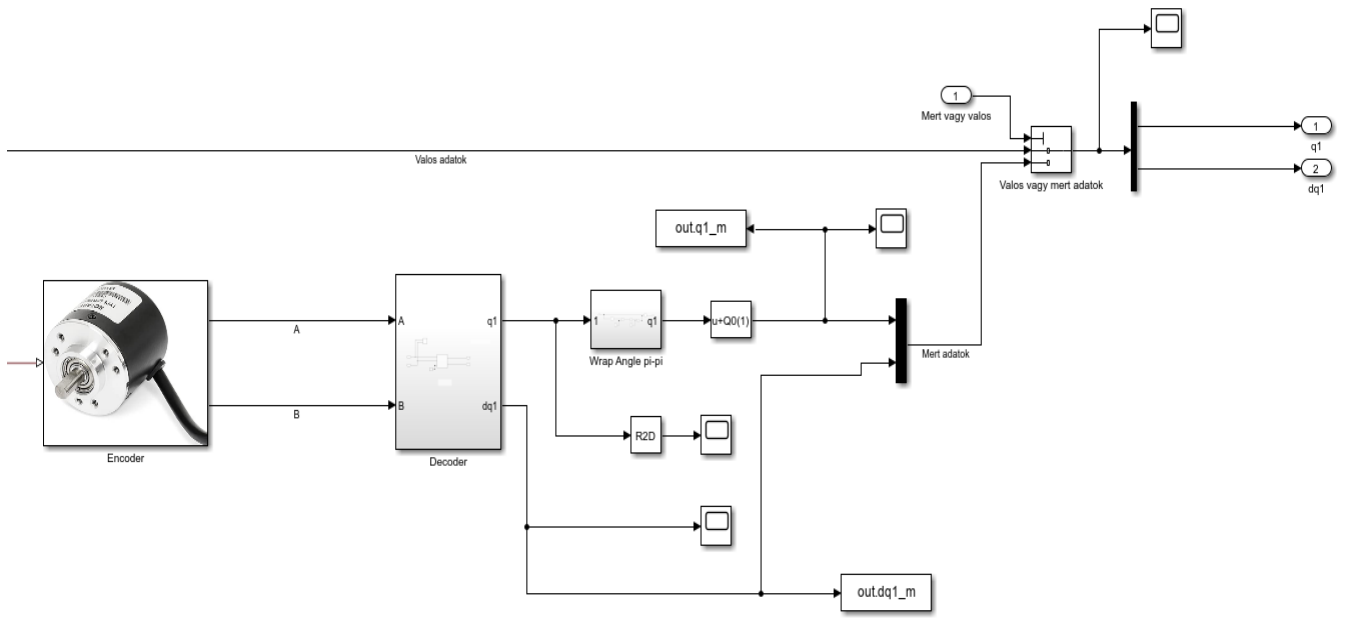
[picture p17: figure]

### 7.6. ábra. Az enkóder és az első csukló Simscape modellje

Itt is megtalálható a forgóérzékelő Simscape modellje[20], illetve egy dekóder is, ami az A és B négyszög jeleket dolgozza fel és számolja ki a diszkrét szöget és szögsebességet. Látható továbbá itt is a második kapcsoló, amivel válthatunk a Simulink által generált adatok és a forgóérzékelő és dekóder által szolgáltatott adatok között.

7.2 Eredmények
A valós rendszer paraméterei szerint elvégeztem a szimulációt, a kezdőállapot: XX0 = [0.1 0 0 0]. Ha

a rendszer kedőállapotát a [0 0 0 0] -ban határozzuk meg, akkor nem fog onnan kimozdulni, tehát érdemes megadni egy minimális 0-tól különböző kezdőállapotot. Ezzel a kezdeti feltornáztató szakasz időbeli hossza is rövidül. A fejlesztőkörnyezetben nyomon lehetett követni a rendszer viselkedését
(7.7. ábra).

### 7.7. ábra. Az acrobot 3D-s modellje szimuláció közben

A (7.8. ábra) ábrán láthatunk egy sikeres feltornászást és stabilizálást az UEP pont körül, csillaggal jelölve a váltás időpontját a feltornászást végző szabályzóról a stabilizálást végző lineáris szabályzóra.

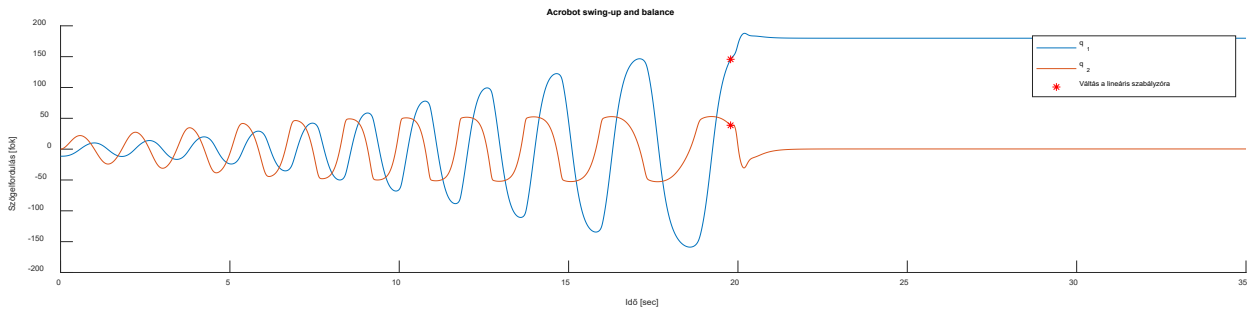
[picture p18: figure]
Idő [sec]; Szögelfordulás [fok]; Acrobot swing-up and balance; Váltás a lineáris szabályzóra

7.8. ábra. Az acrobot szögeinek és szögsebességeinek változása időben egy sikeres szabályzás alatt

A (7.9. ábra) ábrán láthatjuk a rendszer összenergiáját a szabályozás ideje alatt. A célenergia értéke 1.16 J, vagyis csakis a rendszer potenciális energiája az inverz helyzetében.

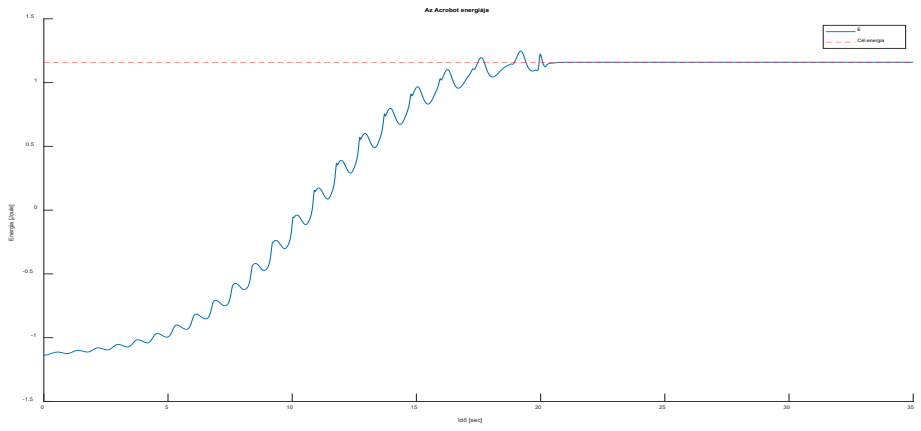
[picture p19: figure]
Idő [sec]; Energia [Joule]; Az Acrobot energiája; Cél energia

### 7.9. ábra. A teljes rendszer energiája és a cél energia a szabályozás alatt

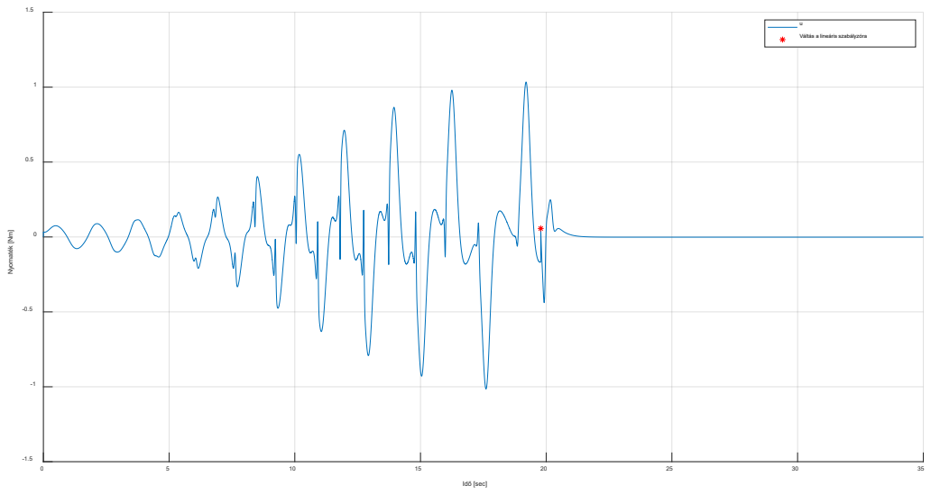
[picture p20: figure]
Idő [sec]; Nyomaték [Nm]; Váltás a lineáris szabályzóra

### 7.10. ábra. A szabályzó jel változása Nm-ben a szabályozás közben

A (7.10. ábra) látható a szabályzó jel, vagyis a második csuklóra ható nyomaték. Ezt a fizikai rendszeren nem tudjuk közvetlenül ráadni a rendszerre a szervomotorral, ott az előírt pályát követi a rendszer.

### 7.11. ábra. Az acrobot fázisportréja, az első szegmens szögelfordulása és szögsebesség

függvényében
A (7.11. ábra)-n látható a fázisportré egy része a teljes szabályozási szakasz alatt. Az első szegmens szögsebessége látható a szögelfordulás függvényében. Látható, ahogy a 0 közeli kezdeti állapotból eléri az instabil egyensúlyi helyzetét, 180 °-ot, 0 sebességgel.

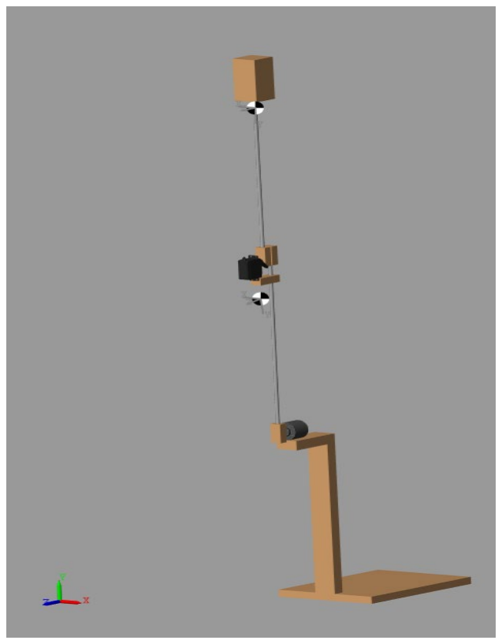
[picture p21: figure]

### 7.12. ábra. Az acrobot 3D-s modellje a felső inverz pontjában

7.3 Modellezés DC motorral

Ahogy a (bevezetőben vagy hol) említettem a gyakorlati megvalósítás során a szervomotornak előnyei és hátrányai is vannak. Egy másik megoldás lehet az egyenáramú motorok használata egy fogaskerék áttételt használva a kellő nyomaték eléréséhez. Ennek a hátránya a motor ára, mivel egy viszonylag kis méretű motorral kell elérni akkora nyomatékot, ami eltudja fordítani a második szegmenst, a rajta levő súllyal együtt. Másik hátránya a nehezebb gyakorlati szabályozása, mivel nyomatékszabályozást kell végezni, nem a tengely sebességét kell szabályozni, hanem az azon megjelenő nyomatékot. Amint a (7.10. ábra)-n látható a szabályzójel, vagyis a nyomaték időben gyorsan változik, ezt a nyomatékot kell előállítani a motor tengelyén is, lehetőleg úgy, hogy a tranziensek hatása minél kisebb legyen. Ennek tanulmányozására elkészítettem a Simulink környezetben a modell szabályozását a szervomotor helyett egy egyenáramú motort használva (7.13. ábra).

A modellezésben a Simscape által megadott általános DC motor modelljét használtam, ehhez csatlakoztatva egy nyomatékváltót 150:1 arányú áttétellel. Egy feszültség-, és árammérővel mérem a motoron sarkain levő feszültséget, illetve a motoron átfolyó áramot. A Simulinkben használt DC

### 7.13. ábra. Egyenáramú motor szabályozása Simulinkben

motor kimenetén egy ú.n. “Rotation” mennyiség jelenik meg, ezért szükséges azt nyomatékká alakítani ahhoz, hogy kompatibilis legyen a modell többi részével, továbbá itt is mérem a szögelfordulást és a szögsebességet.

A szabályozás elve az, hogy a motornyomaték arányos a motoron átfolyó áramerősséggel.[21]

# TT = kkTT ∙ II

( 28 )

T a motor tengelyén megjelenő nyomaték Nm-ben kifejezve, kT a motor nyomaték állandója [Nm/A], és I a motoron átfolyó áramerősség [A].

Az arányosságot a motornyomaték állandó határozza meg, ami minden motornál különböző lehet. Ezt meglehet határozni a katalógus adatok, vagy mérések alapján. Ideális esetben a nyomaték szabályozását egy áramszabályzóval lehet megvalósítani, viszont mivel ez a gyakorlatban nehezen kivitelezhető, ezért már a modellben is a feszültséget szabályozom úgy, hogy a mért áram legyen egyenlő a referencia áramerősséggel. A modellben a motornyomaték állandót 0.083 Nm/A -re választottam, tehát ennek az reciprokával való szorzása (12) a nyomatéknak megadja az ennek megfelelő áramerősséget. A szabályozást egy PID szabályzó végzi a 2.táblázat táblázatban látható paraméterek szerint. A szabályzó bemenetére a referencia jel és a mért áramerősség különbsége van csatolva. Fontos, hogy a szabályzó lekövesse a gyors változásokat a referenciajelben, de pontos is legyen a az UEP pont közelében, ezért felel az integráló tag. A feszültség változtatását egy ideális változtatható feszültségforrás végzi.

P 10
I 0.1
D 0.5
2.táblázat. PID szabályzó paraméterei

7.3.1 Eredmények

A szimulációban sikeres volt a szabályozás, az acrobot elérte a felső egyensúlyi pontját, majd ott tudta stabilizálni magát. A (7.14. ábra)-n látható a kiszámított ideális nyomaték és a motor tengelyén megjelenő nyomatékok összehasonlítása. Megfigyelhetőek eltérések a két érték között, de ennek ellenére a szabályzó sikeresen tudta szabályozni a rendszert.

A (7.15. ábra)-n látható a motoron mért feszültség és áram külön ábrázolva. Elsősorban látszik, hogy az áram arányos a nyomatékkal, mert a két jel időbeni változása szinte azonos. A feszültségnél látható egy kiugró érték, ami természetesen csak az elméleti modellben jöhet létre. Ez a két szabályzó közötti váltásnál történik, ahol a nyomaték, nagyon rövid idő alatt az ellenkező irányban kell, hogy elmozdítsa a második szegmenst.

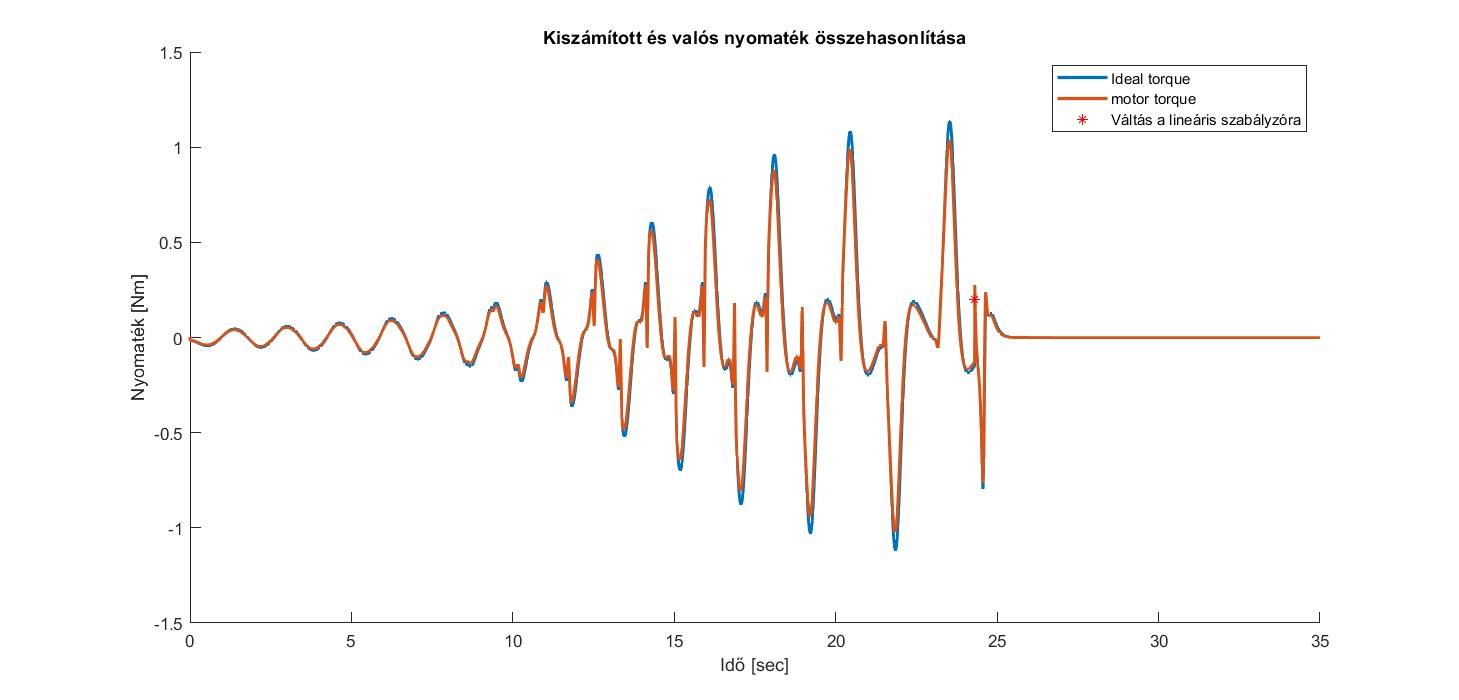
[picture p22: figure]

### 7.14. ábra. Ideális és a motor tengelyén megjelenő nyomatékok összehasonlítása

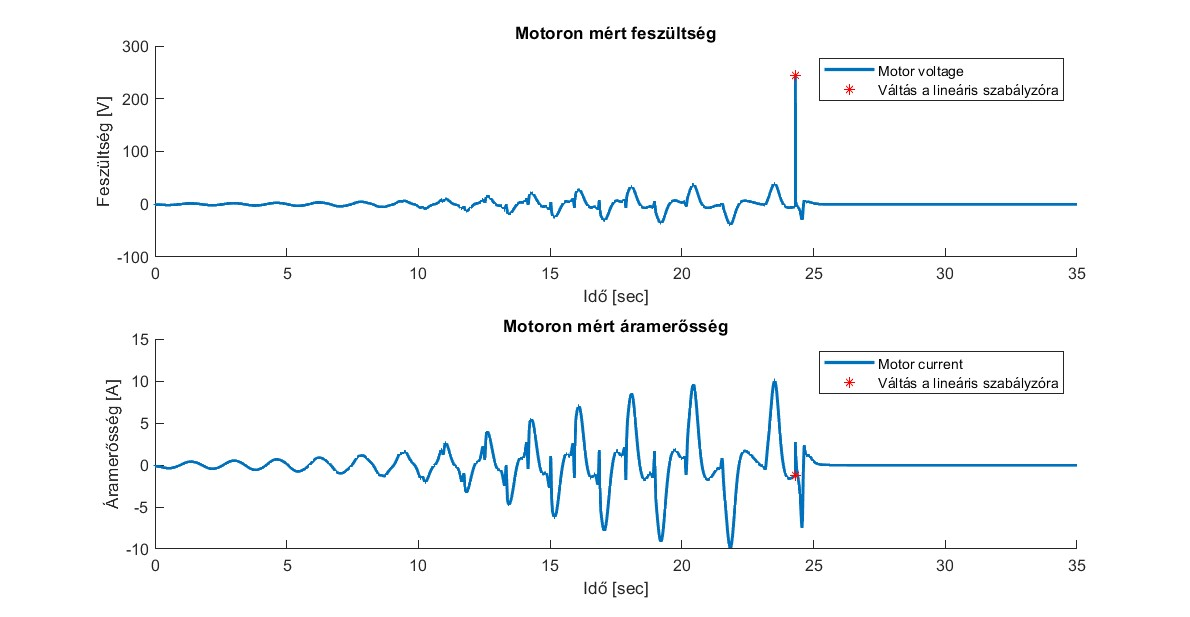
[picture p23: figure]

### 7.15. ábra. Motor áram és feszültség

## 8 Gyakorlati megvalósítás

A (8.1. ábra) ábrán látható az acrobot gyakorlati megvalósítása. A tartószerkezet alsó felében található a szabályozási algoritmust futtató arduino hálózat (8.2. ábra). A tartószerkezet felső felében található a forgóérzékelő, amelyhez rögzítve van maga az acrobot. A szegmensek alumínium rudakból állnak, amelyeknek a végén találhatóak az összekötő elemek. A második szegmens végén található a súly, a nagyobb tehetetlenség elérése érdekében, aminek a tömege 86 gramm. A szervomotorhoz szükséges vezetékek alól vannak elvezetve, mivel nagy mozgási tartományt fed le működés közben.

8.1. ábra. Az acrobot gyakorlati megvalósítása, jobb oldalt a szervomotor és a második csukló

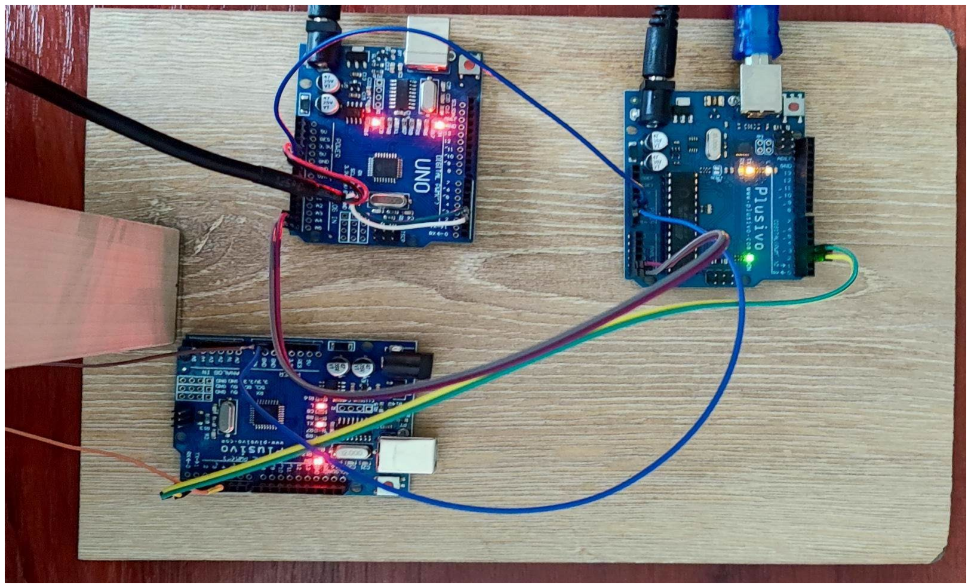
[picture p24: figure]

### 8.2. ábra. Arduino fejlesztőlapokkal megvalósított szabályozás

A 3. táblázatban láthatóak a valós rendszer paraméterei. A szegmensek hosszánál nem csak az alumínium rudak hosszát vettem figyelembe, hanem magának a szegmenseknek a súly középpontját, ugyan úgy ahogy az elméleti acrobot mozgásegyenleteiben is szerepel. A második szegmens végén található egy súly, ami több inerciát ad a rendszernek, így elérve a könnyebb energiapumpálást a rendszerbe, és kompenzálja az első csuklóban található szervomotor tömegét.

Jelölés | Érték | Mértékegység
l1 | 0.4 | m
l2 | 0.425 | m
lc1 | 0.2885 | m
lc2 | 0.34 | m
m1 | 0.1012 | kg
m2 | 0.1203 | kg
I1 | 0.0015 | kg*m²
I2 | 0.0018 | kg*m²

### 3. táblázat. A valós rendszer paraméterei

### 8.1 Szabályozó felépítése

A 8.3. ábra ábrán látható a szabályozás tömbvázlata. Balról az első arduino feladata a forgóérzékelőtől érkező adatok fogadása és azok feldolgozása. Itt kiszámításra kerül a forgóérzékelő által érkező jelekből az első csukló relatív elfordulása a kezdőpozíciójához képest, és ennek a szögsebessége. A második arduino feladata a szabályzó jel kiszámítása a beérkező szög, szögsebesség és a neuronhálók segítségével. Itt a 24. fejezetben részletezett két neuronháló került leimplementálásra, a Matlab programban kiszámolt súlyzók alapján végzem el a mátrix szorzásokat. Mivel kis méretű neuronháló is megtudta tanulni, ezért valós időben gyorsan tud működni a szabályozás. A harmadik arduino feladata a szervomotor irányítása, feladata, hogy az előző egységtől kapott előírt szögre irányítsa a szervomotort. Itt a külön egység alkalmazására legfőképp a Timerek közötti konfliktusok miatt volt szükség.

### 8.3. ábra. A gyakorlati szabályozás tömbvázlata

8.2 Állapotok mérése

A (8.4. ábra) és (8.5. ábra) ábrákon látható a forgóérzékelőtől érkező A és B jel logikai feldolgozása, amelyekből a forgás irányát is meglehet határozni. A forgóérzékelőben 2 tárcsa található, amelyek bizonyos helyeken lyuggatva vannak, így forgás közben egy bizonyos pozícióban vagy átengedik a fényt, vagy nem. Forgás közben ezt egy-egy érzékelő érzékeli, és ennek alapján rendel hozzá egy feszültségszintet, ami lehet 0 vagy 5 Volt. Forgás közben így egy négyszög jelet eredményez. A 2 tárcsa egymáshoz képest relatív el van tolva, ebből lehet meghatározni a forgás irányát.

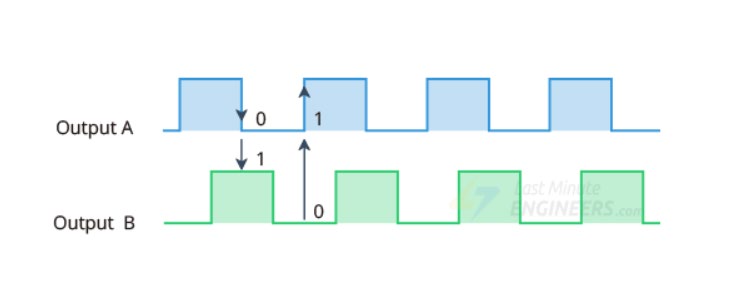
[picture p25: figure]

8.4. ábra. A forgóérzékelő által küldött A és B jelforma, amikor a forgás az óramutató járásával megegyező irányban történik[22]
8.5. ábra. A forgóérzékelő által küldött A és B jelforma, amikor a forgás az óramutató járásával megegyező irányban történik[22]

A szög és szögsebesség mérése egy 600 impulzusos forgóérzékelővel történik. Egy teljes fordulat alatt 600 impulzust ad le, A és B fázisban, melyek 90°-kal vannak eltolva egymáshoz képest. A feldolgozás során a két jel helyzetéből kitudom számítani a forgás irányát. Az A fázis lefutó élére nézem meg a B értékét. (2.függelék) Ha az 1, akkor az óramutató irányába forog, ha 0 akkor azzal ellentétesen. Ezt a logikát alkalmazom a B jelre is, ott az A jel értékét figyelem, a B jel lefutó élére, ezzel megduplázva a felbontást. Mindegyik lefutó él egy megszakítást generál az arduinon, ezzel elérve, hogy mindegyik jelet figyelembe vegye. A processzor minden 20ms-onként kiszámolja a relatív szögelfordulást és a szögsebességet (3.függelék). Mivel ebben az esetben egy fordulat 1200 impulzust tartalmaz, ezért minden lefutó él 0.3°-t jelent. A sebesség mérése a (29) képlettel történik, ahol a mintavételezési idő[t]

20ms.[23] Az n jelöli a beérkezett pulzusok számát, összeadva az A és B vezetéken érkező jeleket. N a pulzusok száma egy teljes kör alatt (1200). Egy 600 impulzusos forgóérzékelőt használtam, és mivel mind a két beérkező négyszög jelet felhasználtam, így 1200 impulzus érkezik be egy fordulat alatt.

# ωω = 2ππππ

NN

( 29 )

8.3 Vezérlőjel számítás

A számításokat külön arduino végzi. Itt került implementálásra a két szabályozásnak megfelelő egyszerű neuronháló és a köztük való váltást eldöntő logika. A neuronháló megvalósítása (1.függelék):

- Preprocess, adatok skálázása
- Inger kiszámítása
- Aktivációs függvény alkalmazása
- Rejtett réteg ingerének kiszámítása
- Purelin aktivációs függvény alkalmazása
- Process output, végeredmény skálázása

A Matlabban kiszámolt súlyzók értékeit használom. A számítások elkezdése előtt szükség van az adatok skálázására, ami egy maximum és minimum érték közé skálázza be a 2 bemenetet, vagyis a szögpozíciót és a szögsebességet. Ezután történik a súlyzókkal való szorzás, majd az aktivációs függvény (szigmoid) alkalmazása. Ezután kiszámításra kerül a rejtett réteg ingere. A következő aktivációs függvény után (purelin), ami egy lineáris aktivációs függvény, történik meg a végeredmény skálázása.

Mivel, a gyakorlati fázisban a 2. csukló állapotai nincsenek mérve, ezért a két szabályozás közötti váltásnál egy egyszerűbb feltételt alkalmazok. Ennek az alapja az, hogy akkor vált át a lineáris szabályzóra, ha az első csukló pozíciója a kezdőpozícióhoz képest 180° és a sebessége is minimális.

8.4 Szervo motor vezérlés

A szervomotor belsejében található egy belső szabályzó áramkör (PID szabályzó). Ennek segítségével képes pontos szögpozícióra beállni. Ennek az irányítása egy pwm jellel történik, amely 50 Hz frekvenciájú. A kitöltési tényező változtatásával lehet vezérelni a motort. A szervomotor 180°-t képes fordulni. Az 1ms-os kitöltési tényező a minimális -90°-k felel meg, 2ms a 90°-k. A megadott kitöltési tényező és a szervomotor szöge egyenesen arányos a két szélsőérték között, tehát ennek alapján bármilyen szöget be tudunk állítani 5 microsecundumos pontossággal. Az arduinon ezt a Servo.h könyvtár segítségével oldottam meg. Itt megadva a kívánt szöget, automatikusan kiszámítja a szögnek megfelelő kitöltési tényezőt, és beállítja az adott timereket. A Timer1-et az 50Hz-es jel létrehozásához, a Timer2-t a kitöltési tényező pontos megadásához használja a rendszer.

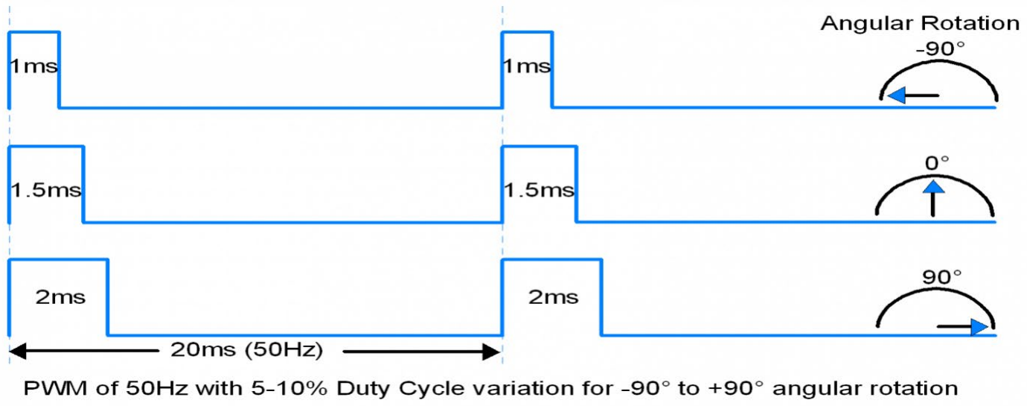
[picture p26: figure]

8.6. ábra. 50Hz-es PWM jel a szervomotor irányításához, feltüntetve a két szélső és a középső állapotához szükséges kitöltési tényezőt[24]

8.5 Kommunikáció

A szabályozás megvalósításához 3 külön egységet használtam. Ennek a főbb okai: a feladatok elkülönítése, jobb átláthatóság, a Timerek közötti konfliktusok, ütközések elkerülése, könnyebb fejleszthetőség a későbbiekben.

Az első és második arduino között i2C kommunikációs protokollt használok, a Wire.h könytárat használva.[25] Az első, forgóérzékelőtől érkező jeleket feldolgozó egység a Master. 20ms-ként küld el egy union típusú adatot, ami tartalmaz 2 float típusú számot, 8 byte-t küld el összesen.

A Slave-ben minden küldéskor aktiválódik egy megszakítás, ami elmenti a küldött tömb első, és második 4 byte-át külön változókba, amik jelentik a kiszámított aktuális szögelfordulást és szögsebességet.

A második és harmadik egység között soros kommunikációt használok. Az arduinon ezeket az RX és TX pinek segítségével lehet megvalósítani. Az eszköz ezek segítségével kommunikál a számítógéppel is, ezért a mérések elvégzése érdekében a számításokat végző arduinon szoftveresen hoztam létre az RX és TX pineknek megfelelő 2,3-as digitális pineket, a SoftwareSerial könyvtárral.[26] A protokoll csomagokat állít össze, amely tartalmaz egy start bitet, az adatot, paritás bitet, stop bitet, majd bitekké darabolva küldi el.

Miután a fogadó fél megkapta a biteket, visszaállítva azokat az UART bufferben tárolja, onnan kiolvasva tárolja el egy változóban. A küldött adat a kiszámított előírt szög float típus, 4 bájton ábrázolva.

## 9 Gyakorlati eredmények

A számításokat végző arduinot a számítógéphez csatlakoztatva tudtam mérni az állapotokat, és a kiszámolt vezérlő jelet. A maximális szög, amit elér a feltornászási fázisban 100.8° (9.1. ábra). A mérést -57° kezdő pozícióból kezdtem, mivel a 0 körüli szögekre, a szervomotor nem tudja időben lekövetni az előírt pályáját, ezért beremeg a rendszer és időben csak később kezdődik el a swing-up fázis.

A rendszer nem tudja elérni az UEP pontját, viszont látható, hogy a lengések amplitúdója fokozatosan nő. Legfőképp a fizikai határai miatt nem tudja elérni az UEP pontját, a továbbiakban szükséges lesz a vezetékek meghosszabbítása, és a tartószerkezet stabilabbá tétele, rögzítése, hogy minimális legyen annak az energia elnyelése.

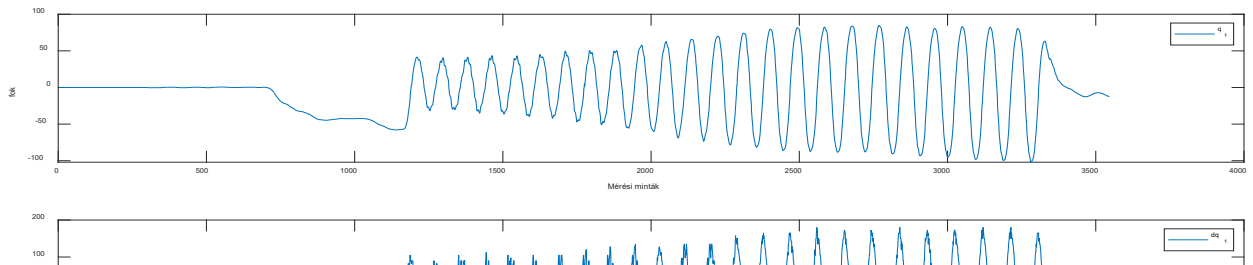
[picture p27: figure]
Mérési minták; fok

### 9.1. ábra. A megvalósított rendszer mérési eredményei szabályozás közben

A (9.2. ábra) ábrán látható összehasonlítva a leszimulált rendszer és a valós mérés. Megfigyelhető, hogy csak több idő után tud kilépni a 0° környékérő a valós rendszer, mivel berezeg.

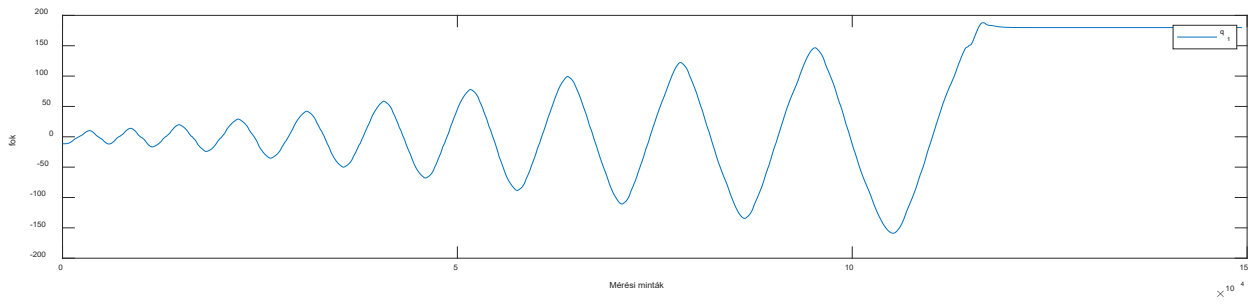
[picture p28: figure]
Mérési minták; fok

9.2. ábra. Feltornáztatási fázis összehasonlítása. Valós rendszer (felső). Szimulált, elméleti modell (alsó)

## 10 Összegzés, következtetések

A dolgozat célja egy alulaktuált rendszer, az acrobot szabályozása, és annak bemutatása. Látható, hogy e rendszerek szabályozása a valóságban sokkal nehezebb, mint például az acroboté is.

Összességében sikerült megépíteni egy szerkezetet, ami eleget tesz egy alulaktuált rendszer követelményeinek, és jól megközelíti az elméleti acrobot sajátosságait. Elkészült ennek a részletes 3D-s modellje, amin sikerült megvalósítani és bemutatni a ‘swing up and balance’ szabályozást.

A programban lehetőség van a paraméterek változtatására is, tehát felhasználható a későbbi szimulációk során is, amennyiben változtatások történnek a valós rendszeren.

Jövőbeni cél a szerkezet stabilabbá tétele, tovább minimalizálva a másfajta mozgásokból eredő energiaveszteséget. Másik cél egy a 7.3. fejezetben részletezett DC motor beépítése és a szerkezet azzal való szabályozása. Ehhez a továbbiakban szükséges egy nyomatékszabályozást megoldani, ami által mindig a szabályzás által kiszámolt megfelelő nyomaték fog megjelenni a motor tengelyén.

Továbbfejlesztési lehetőségek a valós acroboton még a megfelelő motor kiválasztásában, beszerelésében és annak a szabályozásának a megoldásában vannak.

Ismerve a valós rendszer paramétereit lehetővé vált másfajta szabályozások tanulmányozása, úgy a gyakorlatban, mint ideális környezetben a Matlabon belül. A Matlabban és Simulink környezetekben elkészített program által le lehet modellezni a valóságban meglévő acrobot viselkedését különböző szabályzó jelek hatására. A program és a Simulink modellek is elkülönítve, strukturálva vannak, tehát alkalmas arra, hogy akár a későbbiekben is másfajta szabályozásokat is be lehessen építeni.

## Köszönetnyilvánítás

Ezúton szeretnék köszönetet mondani konzulens tanáromnak, dr. Dávid Lászlónak, a mentorálásért és iránymutatásokért a dolgozat elkészítése közben.

## 11 Irodalomjegyzék

[1] Bodor Bálint, “Alulaktuált robotok szabályozásának eltérő megközelítései TDK dolgozat,” 2015.
[2] Mark W. Spong, “The Swing Up Control Problem For The Acrobot,” 1995.
[3] M. W. Spong, “Swing Up Control of the Acrobot *.”
[4] R. Tedrake, “Underactuated Robotics: Learning, Planning, and Control for Efficient and Agile Machines Course Notes for MIT 6.832,” 2009.
[5] G. Boone, “Efficient Reinforcement Learning: Model-based Acrobot Control,” 1997. [Online]. Available: www.cc.gatech.edu/-gboone
[6] X. Xin and T. Yamasaki, “Energy-based swing-up control for a remotely driven acrobot: Theoretical and experimental results,” IEEE Transactions on Control Systems Technology, vol. 20, no. 4, pp. 1048– 1056, 2012, doi: 10.1109/TCST.2011.2159220.
[7] R Nave, “Moment of Inertia: Rod.” http://hyperphysics.phy-astr.gsu.edu/hbase/mi2.html#irod (accessed Apr. 17, 2023).
[8] Russ Tedrake, “Multi-Body Dynamics.” http://underactuated.mit.edu/multibody.html#double_pendulum (accessed Apr. 17, 2023).
[9] Márton Lőrinc, “Robotokarok Dinamikus Modellezes Palyatervezes PDG PID.”
[10] Matthew Peter Kelly, “MatthewPeterKelly / OptimTraj.” https://github.com/MatthewPeterKelly/OptimTraj (accessed Jun. 16, 2023).
[11] M. W. Spong, “Underactuated Mechanical Systems.”
[12] X. Xin and M. Kaneda, “A Robust Control Approach to the Swing up Control Problem for the Acrobot,” 2001.
[13] D. N. Kutasi and L. Márton, Rendszerelmélet laboratóriumi gyakorlatok. Scientia, 2010.
[14] György Katalin, “Diszkrét LQR állapot utáni szabályzó laborgyakorlat.”
[15] X. Xin and M. Kaneda, “Analysis of the energy-based swing-up control of the Acrobot,” International Journal of Robust and Nonlinear Control, vol. 17, no. 16, pp. 1503–1524, Nov. 2007, doi: 10.1002/rnc.1184.
[16] “Matlab feedforwardnet.” https://www.mathworks.com/help/deeplearning/ref/feedforwardnet.html (accessed Apr. 17, 2023).
[17] “Matlab Simscape.” https://www.mathworks.com/products/simscape.html (accessed Apr. 17, 2023).
[18] “Matlab ode23”, Accessed: Apr. 17, 2023. [Online]. Available: https://www.mathworks.com/help/matlab/ref/ode23t.html
[19] “MG996R servo.” https://datasheetspdf.com/pdf/942981/ETC/MG996R/1 (accessed Jun. 19, 2023).

[20] “Optical Rotary Encoder.” https://grabcad.com/library/optical-rotary-encoder-1/details?folder_id=13312851 (https://grabcad.com/library/optical-rotary-encoder-1/details?folder_id=13312851) (accessed Apr. 17, 2023).
[21] “Motor torque.” https://www.motioncontroltips.com/faq-difference-between-torque-back-emf-motor-constant/ (https://www.motioncontroltips.com/faq-difference-between-torque-back-emf-motor-constant/) (accessed Jun. 13, 2023).
[22] “How Rotary Encoder Works and Interface It with Arduino.” https://lastminuteengineers.com/rotary-encoder-arduino-tutorial/ (accessed Apr. 17, 2023).
[23] “How are encoders used for speed measurement?” https://www.motioncontroltips.com/how-are-encoders-used-for-speed-measurement/ (https://www.motioncontroltips.com/how-are-encoders-used-for-speed-measurement/) (accessed Apr. 17, 2023).
[24] “Servo Motor.” https://www.electronicwings.com/sensors-modules/servo-motor (accessed Apr. 17, 2023).
[25] “How to Setup I2C Communication on the Arduino.” https://www.circuitbasics.com/how-to-set-up-i2c-communication-for-arduino/ (https://www.circuitbasics.com/how-to-set-up-i2c-communication-for-arduino/) (accessed Apr. 17, 2023).
[26] “How to Set Up UART Communication on the Arduino.” https://www.circuitbasics.com/how-to-setup-uart-communication-for-arduino/ (https://www.circuitbasics.com/how-to-set-up-uart-communication-for-arduino/) (accessed Apr. 17, 2023).

## 12 Függelék

### 1) Neuronháló implementálása (Arduino/Compute.io) // implementation of the pretrained neural network // Swing up float MLP_swing_up(float q1, float dq1)

{

### // preprocess q1

xq1 = ((q1 - sw_I_xmin) * sw_I_gain) + sw_I_ymin;

### // Input layer

v = (sw_Iw1 * xq1 + sw_Iw2 * dq1) + sw_b1;
u = 2 / (1 + exp(-2 * v)) - 1;

### // Hidden layer

v = (sw_Lw * u) + sw_b2;

### // purelin activation function // Process output uv = v + 1; // O_min

uv = uv * sw_O_gain;
uv = uv + sw_O_xmin;
return uv;
}

### 2) Enkóder pozíció számolás (Arduino/High_speed_encoder.io) void ai0() { // ai0 is activated if DigitalPin nr 2 is going from HIGH to LOW // Check pin 3 to determine the direction

vel_cnt++;

### if (PIND & B00001000)

{
counter--;
}

## else

{
counter++;
}
}

### 3) Enkóder sebesség számolás

### ISR(TIMER1_COMPA_vect)

{
vel_cnt = counter - vel_cnt_old;

### ENC_angle = 0.3 * counter; // 0.3 = 360/1200 - degree ENC_vel = (2 * 3.14 * vel_cnt) / (1200 * 0.02); // | 0.02 -> 50Hz ENC_vel = ENC_vel * 57.29; // rad/sec to degree/sec

vel_cnt_old = counter;

### // reset the angle if (ENC_angle > 360)

counter = 0;

### if (ENC_angle < -360)

counter = 0;

### // Send the value of counter

converter.q1[0] = ENC_angle; converter.q1[1] = ENC_vel; }

### 4) Matlab szimuláció fő program (Acrobot_Pololu_Simulation/Main.m)

%% Betölti a valós rendszer paramétereit
run('real_parameters.m');

%% Linearizálas a munkapont körül
% q1 q2 dq1 dq2
[A,B] = linearizalas(m1,m2,l1,l2,lc1,lc2,J1,J2);

%% LQR számítás
K = LQR_function(A,B);

%% Szimuláció Simulinkben
open_system('Real_Acrobot_Simulation.slx') Sim_time = 40;
out = sim('Real_Acrobot_Simulation',Sim_time);

% set view convention -> Y up (XY)
% standard views -> Front view

%% Szimulációs eredmények elmentése run('getParameters.m');

%% Ábrák megjelenítése
run('Visualization_real.m');

### UNIVERSITATEA SAPIENTIA DIN CLUJ-NAPOCA FACULTATEA DE ȘTIINȚE TEHNICE ȘI UMANISTE, TÎRGU-MUREȘ SPECIALIZAREA AUTOMATICĂ ȘI INFORMATICĂ APLICATĂ

Vizat decan | Vizat director departament
Conf. dr. ing. Domokos József | Ș.l. dr. ing Szabó László Zsolt

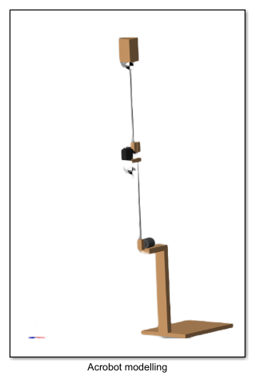
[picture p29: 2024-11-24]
media/Main_01.png

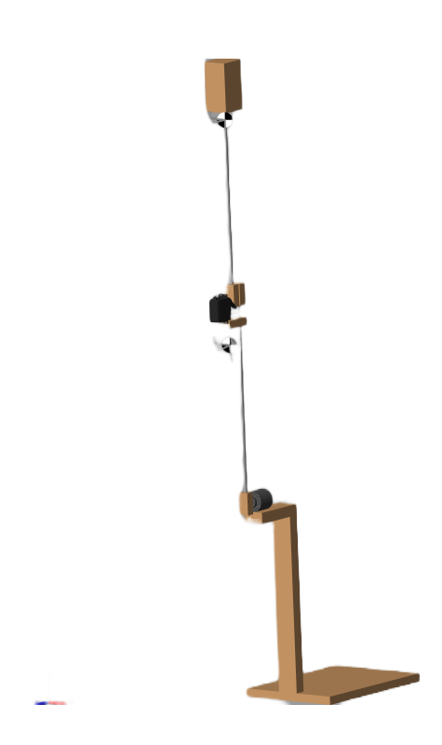
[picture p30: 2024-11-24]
Acrobot_Simulation/img/Acrobot_main.png

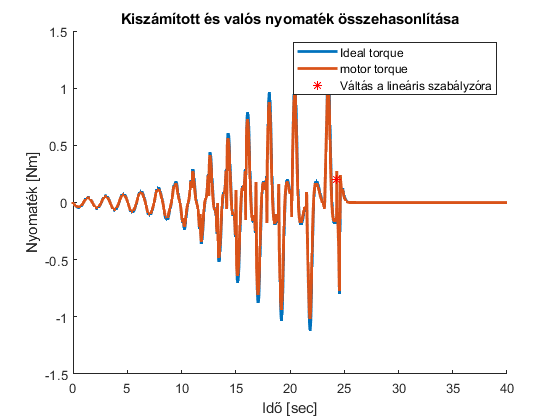
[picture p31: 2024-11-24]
media/Main_07.png

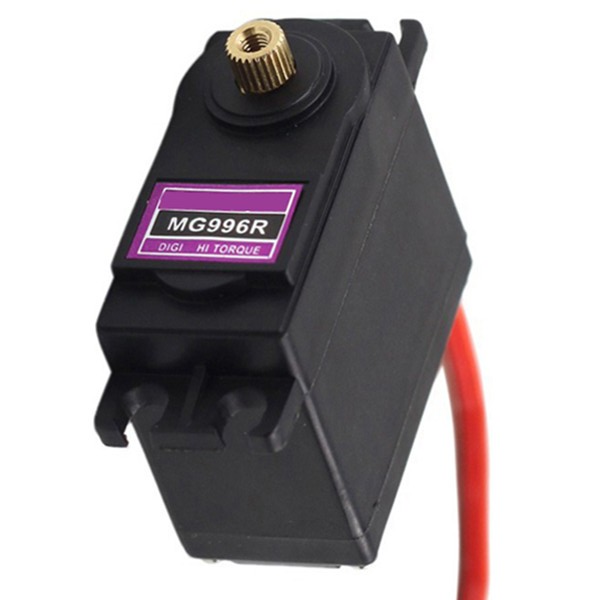
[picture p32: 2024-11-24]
Acrobot_Simulation/img/servo/MG996R.png

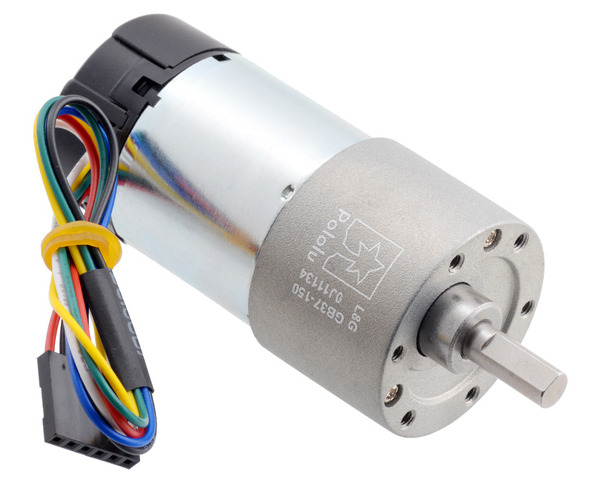
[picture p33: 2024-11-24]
Acrobot_Simulation/img/Pololu_motor/pololu.jpg

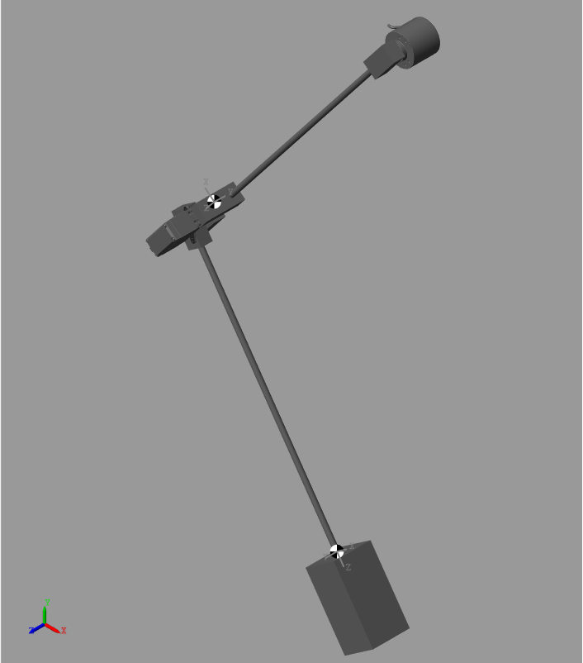
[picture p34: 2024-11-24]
Acrobot_Simulation/img/Modell1.png

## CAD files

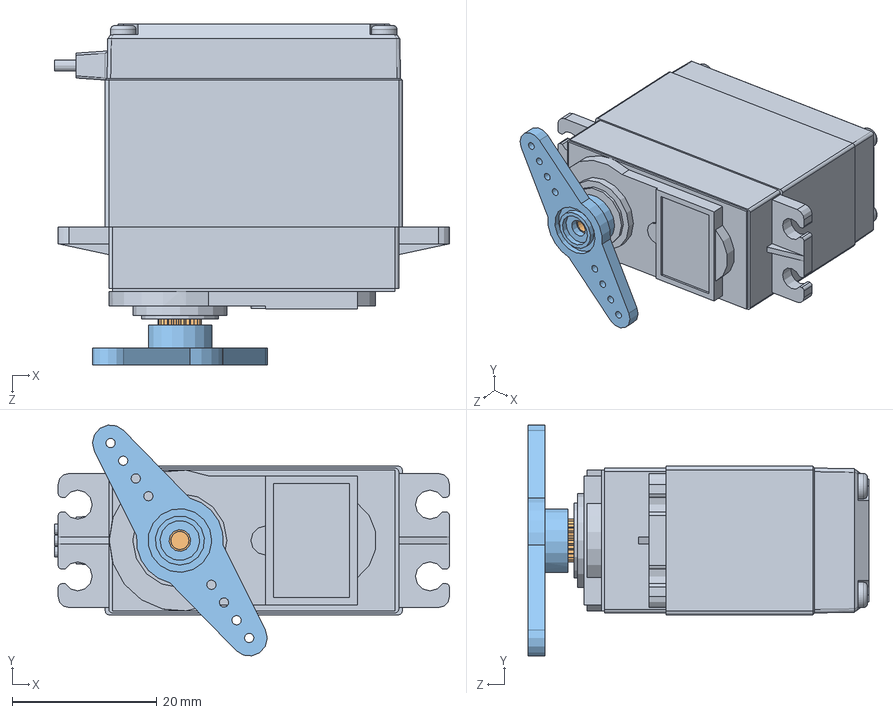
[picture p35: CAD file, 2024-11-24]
Acrobot_Simulation/img/servo/MG996R SBORKA.SLDASM
54.5 x 31.8 x 47.0 mm
Servo MG996R
Servo MG996R Shaft
Servo MG996R arm01

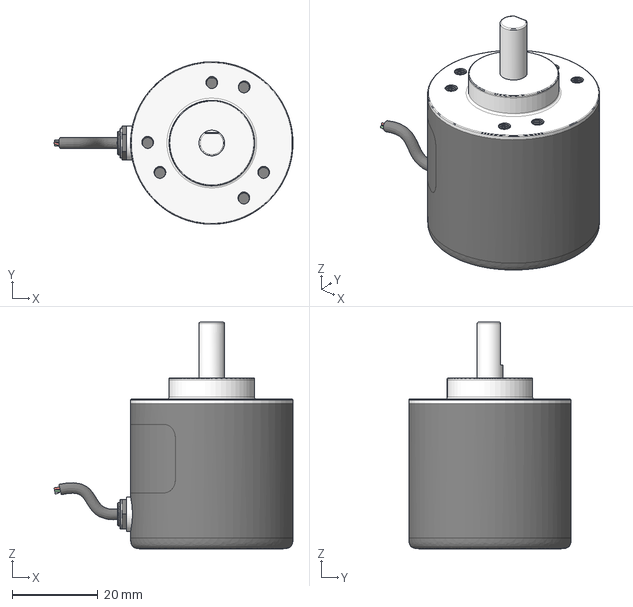
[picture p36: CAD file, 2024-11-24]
Acrobot_Simulation/img/encoder/ORANGE_ENCODER_600PPR v1.step
55.9 x 38.0 x 53.0 mm

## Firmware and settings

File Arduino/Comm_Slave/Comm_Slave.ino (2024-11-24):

// Servo Motor Driver
// Serial Communication Reciever

#include <Servo.h>

// Servo Motor Object
Servo servo_1;

int servo_pin = 5; // PWM pin for servo control
int pos = 90;    // servo starting position

volatile float u = 0.0;

void setup() {
  Serial.begin (9600);

  // Servo
  servo_1.attach(servo_pin); // start servo control
  servo_1.write(pos);  // 0 - 180, start at 90 degree

}


void loop() {

  if (Serial.available() >= sizeof(float))
  {
    // Read the q2 postiton for the servo
    Serial.readBytes((byte*)&u, sizeof(float));
  }

  servo_1.write(u + 90 - 5); // Send pwm signal for the servo (-5 compensation)

}

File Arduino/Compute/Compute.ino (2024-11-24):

// Compute the control signal for the servo
// and send it to tha next Arduino
// Serial Communication Sender

#include <Wire.h>
#include <SoftwareSerial.h>
// #include <math.h>  // acrtanhoz

// Serial Communication
#define RX_PIN 2
#define TX_PIN 3

// using softserial for leaving free the
// hardware serial port for communication with laptop
SoftwareSerial swSerial(RX_PIN, TX_PIN);

// union type for storing 2 float from the sender
union floatToBytes {

  char buffer[8];
  float q1[2];

} converter;

// union type for storing 1 float for the reciever
union floatToBytesSend {

  char buffer[4];
  float uv;

} converter2;

// MLP LQR weights, parameters
const float Iw = 0.0666;
// Iw2 = 0;
const float b1 = -0.5576;
const float b2 = -10.0620;
const float Lw = -19.9388;
const float I_xmin = -24.7058;
const float I_gain = 0.0353;
const int I_ymin = - 1;
const int O_ymin = - 1;
const float O_gain = 77.6853;
const float O_xmin = -90.0623;


// MLP swing up weights, parameters
const float sw_Iw1 = 0.0253;
const float sw_Iw2 = 0.0108;
const float sw_b1 = -0.0087;
const float sw_b2 = -0.0015;
const float sw_Lw = 0.9572;
const float sw_I_xmin = -359.9704;
const float sw_I_gain = 0.0037;
const int sw_I_ymin = - 1;
const int sw_O_ymin = - 1;
const float sw_O_gain = 52.8646;
const float sw_O_xmin = -52.8691;


volatile float v = 0.0;
volatile float xq1 = 0.0;



volatile float u = 0.0; // temporary control signal
volatile float uv = 0.0; // control signal to send

//volatile int servo_cnt = 0;

volatile float q1 = 0;
volatile float dq1 = 0;


void setup() {
  Serial.begin (9600);

  // Start the I2C Bus as Slave on address 9
  Wire.begin(9);
  // Attach a function to trigger when something is received.
  Wire.onReceive(receiveEvent);
  swSerial.begin(9600);

}

// recieve event for reading 8 byte
void receiveEvent(int bytes) {

  uint8_t index = 0;

  while (Wire.available()) {
    converter.buffer[index] = Wire.read();
    index++;
    if (index == 8)
      index = 0;
  }

}

void loop() {

  q1 = converter.q1[0];  // q1 angle
  dq1 = converter.q1[1]; // dq1 angle velocity

  // Simplied switch logic
  // Blanacing
  if ((q1 > 170) && (q1 < 190))
  {
    uv = MLP_DLQR(q1 - 180);

    // kicsi rezgesek miatt
    /*
      if ((uv < 0) && (uv > -5))
      uv = 0;
      if ((uv > 0) && (uv < 5))
      uv = 0;
    */

  }

  else
    // Swing up
  {
    // arctannal proba
    // uv = ((2*90)/3.14)*57.29*atan(dq1*0.017453); // 2*90 
    // uv = uv*57.29;

    uv = MLP_swing_up(q1, dq1);
  }


  // limiting the servo, including the compensation
  if (uv > 90)
    uv = 90;
  if (uv < -85)
    uv = -85;

  // teszt
  // uv = 0;

  // Send data to the third Arduino over software serial
  swSerial.write((byte*)&uv, sizeof(float));

  byte* byteData = (byte*)&uv; //Convert the float number to a byte array

  delay(5);

  // Write to the serial port for measuring
  Serial.print(q1);
  Serial.print(',');
  Serial.print(dq1);
  Serial.print(',');
  Serial.println(uv);

}


// implementation of the pretrained neural network
// Swing up
float MLP_swing_up(float q1, float dq1)
{
  // preprocess q1
  xq1 = ((q1 - sw_I_xmin) * sw_I_gain) + sw_I_ymin;
  // Input layer
  v = (sw_Iw1 * xq1 + sw_Iw2 * dq1) + sw_b1;
  u = 2 / (1 + exp(-2 * v)) - 1;

  // Hidden layer
  v = (sw_Lw * u) + sw_b2;
  // purelin activation function

  // Process output
  uv = v + 1; // O_min
  uv = uv * sw_O_gain;
  uv = uv + sw_O_xmin;

  return uv;

}

float MLP_DLQR(float q1)
{
  // preprocess
  xq1 = ((q1 - I_xmin) * I_gain) + I_ymin;
  // Input layer
  v = (Iw * xq1) + b1; // inger Iw2 = 0
  u = 2 / (1 + exp(-2 * v)) - 1;

  // Hidden layer
  v = (Lw * u) + b2;
  // purelin activation function

  // Process output
  uv = v + 1; // O_min
  uv = uv * O_gain;
  uv = uv + O_xmin;

  return uv;

}

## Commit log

2024-11-24 Upload project
    [Acrobot_schematic.fzz, MG996R SBORKA.SLDASM, ORANGE_ENCODER_600PPR v1.step]
2024-11-24 Clean code
    [MG996R SBORKA.SLDASM]
